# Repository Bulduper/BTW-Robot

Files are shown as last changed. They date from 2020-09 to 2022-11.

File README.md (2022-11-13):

# BTW-Robot
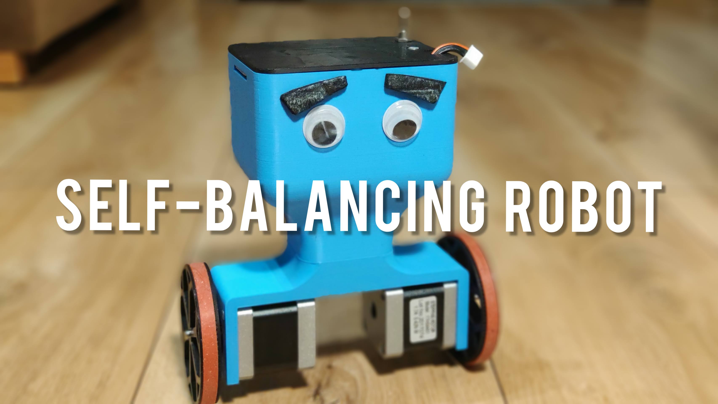
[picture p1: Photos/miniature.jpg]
Photo of robot Balancing robot


## [YouTube video](https://www.youtube.com/watch?v=bfnd0wN4B1s)
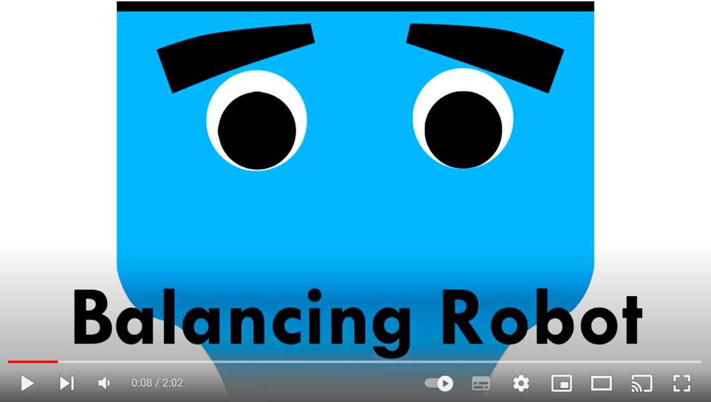
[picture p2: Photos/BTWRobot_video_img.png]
YouTube video (https://www.youtube.com/watch?v=bfnd0wN4B1s)

## Balancing Two-Wheeled Robot
This repository contains all the code files for ESP8266 microcontroller regarding the BTW-Robot project. 

The other part of code is the *android app* to control the robot remotely. [LINK TO REPO](https://github.com/Bulduper/BTW-Robot-Android-App) 

## A short description

The main working principle of a self-balancing robot is to continuously adjust its movement in order to maintain a specific position and/or velocity. 

The BTW-Robot utilizes two stepper motors which are driven to counteract its inertial movement.

## Sensor

The most important information for such a robot is the current angular position.
To get angle data I used MPU6050 inertial measurement unit. The sensor consists of both gyroscope and accelerometer (both 3 Axis).

### Accelerometer
Accelerometer measures acceleration and since under **relatively static** conditions the only significant acceleration is gravitational, we can use that measurement to estimate the tilt angle of the robot.

### Gyroscope
Although the accelerometer would give us a pretty decent estimation of angle in static conditions, the method fails if any oscillations occur.

Gyro measures angular velocity and it does so quite precisely. Precisely enough to be the only source of inertial measurements for our purpouse.
However there are two reasons we cannot use the gyro data alone:
- angular velocity is the derivative of angle and derivatives give no information about starting position. At least once we need to know actual angle, then we could rely on velocity
- gyro measurements tend to drift due to various long term noise (like Coriolis force), so even when no movement the sensor would show changing angle value over time

### Complementary filter
An easy, yet very effective solution is to combine accelerometer and gyro data.
Accelerometer doesn't like high frequecies so we'll give it a low-pass filter.
Gyro doesn't like low frequencies so we'll implement a high-pass filter.
```
angle = c * (angle + gyro * dt) + (1 - c) * accelerometer 
```
where ```c``` would be around 0.98 (depends on time constant).

The above solution is called complementary filter.

## Regulation algorithm
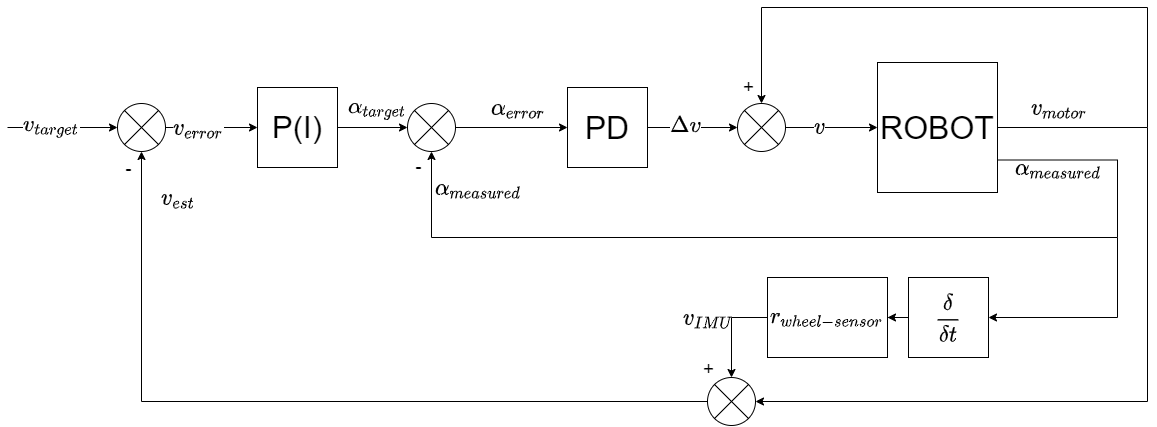
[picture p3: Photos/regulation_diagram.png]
Diagram Regulation algorithm diagram


We've got two closed-loop PID regulators working together in a cascade. The input for the outer regulator is speed error. Error is obtained by subtracting target value and estimated velocity value. The latter involves both absolute motor speed and relative head's speed. This way we can effectively take into account robot tilting as well.
  
## Remote control & telemetry
I used WiFi feature of ESP8266 to remotely control the robot.
Android app sends JSON packets containing steering data via UDP protocol to the ESP. In return ESP sends packets containing speed and tilt values the same way.

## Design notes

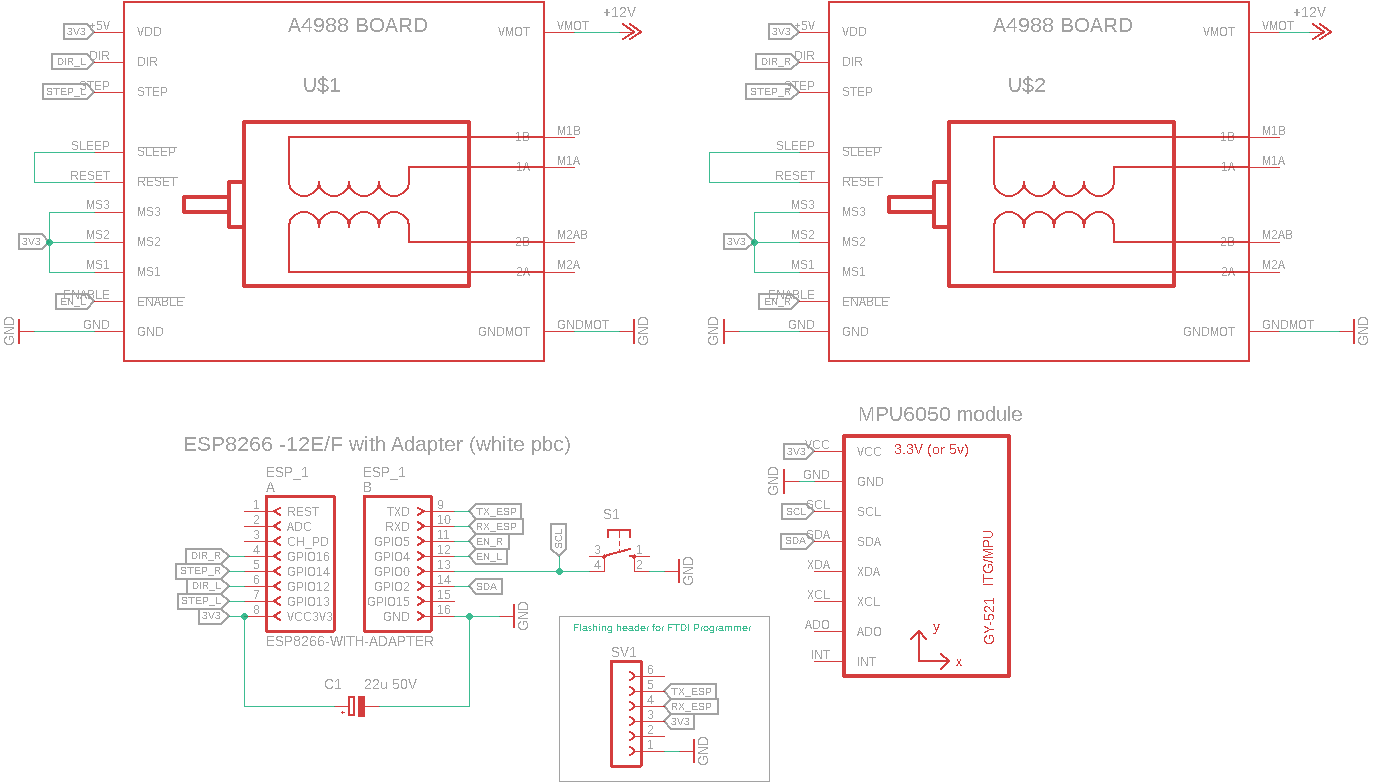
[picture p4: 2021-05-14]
Schematics/BTW_Robot_schematic.png

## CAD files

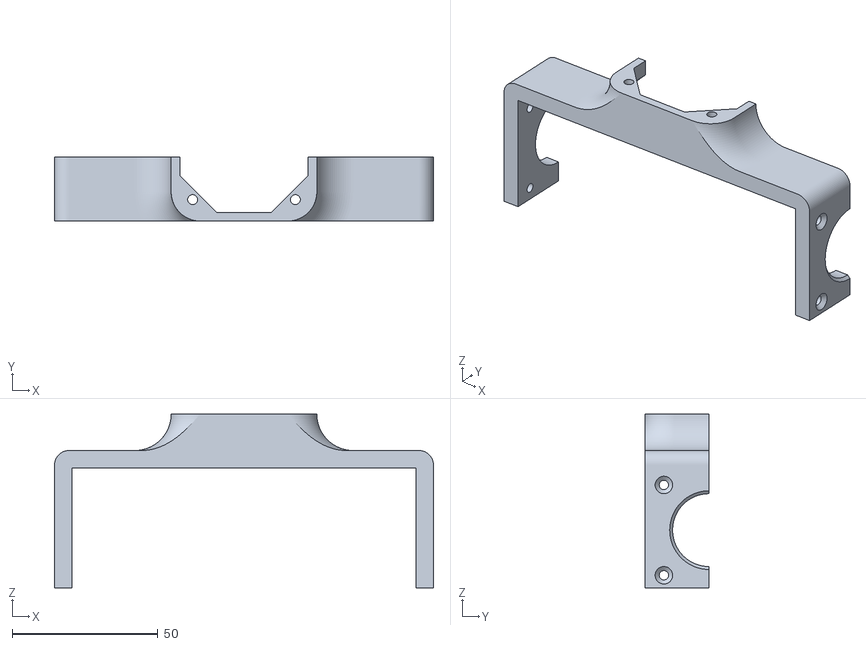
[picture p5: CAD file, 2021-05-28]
STL Files/main_bottom_oneHalf.stl
130.1 x 22.0 x 59.7

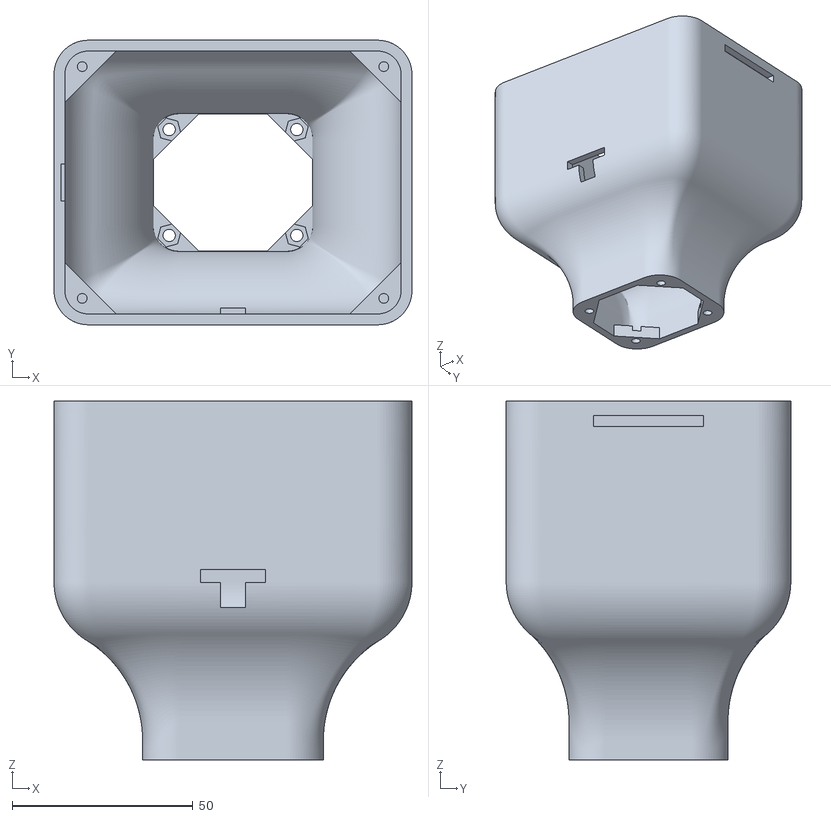
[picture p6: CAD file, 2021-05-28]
STL Files/main_top_v2.2.stl
99.0 x 78.7 x 99.2

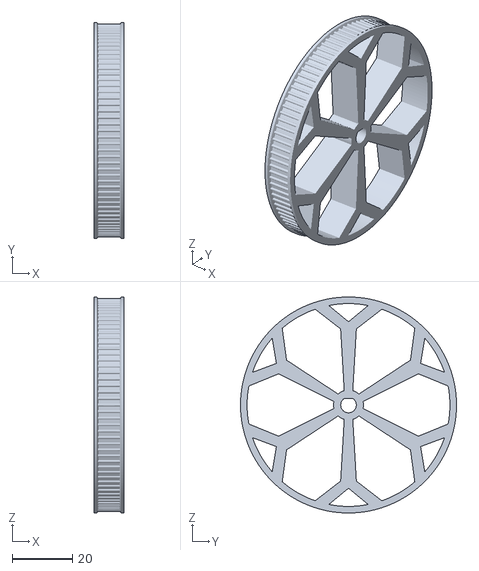
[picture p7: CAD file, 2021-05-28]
STL Files/wheel.stl
10.0 x 72.0 x 72.0

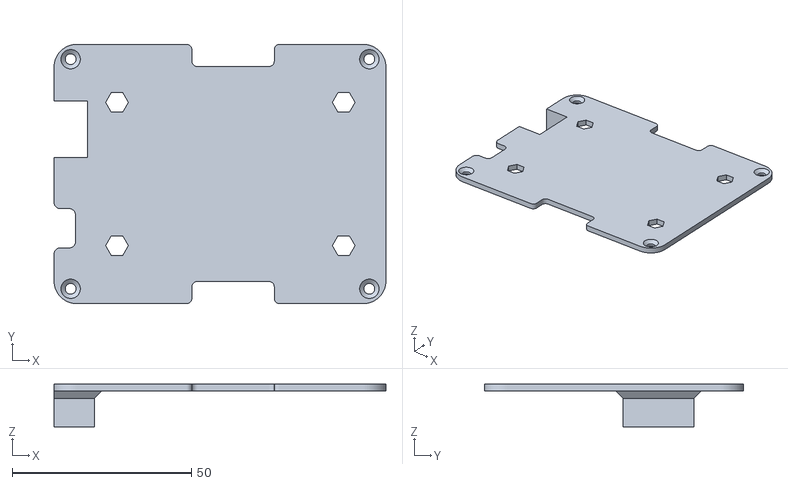
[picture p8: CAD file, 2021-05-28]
STL Files/shelf_v2.2.stl
92.7 x 72.4 x 12.0

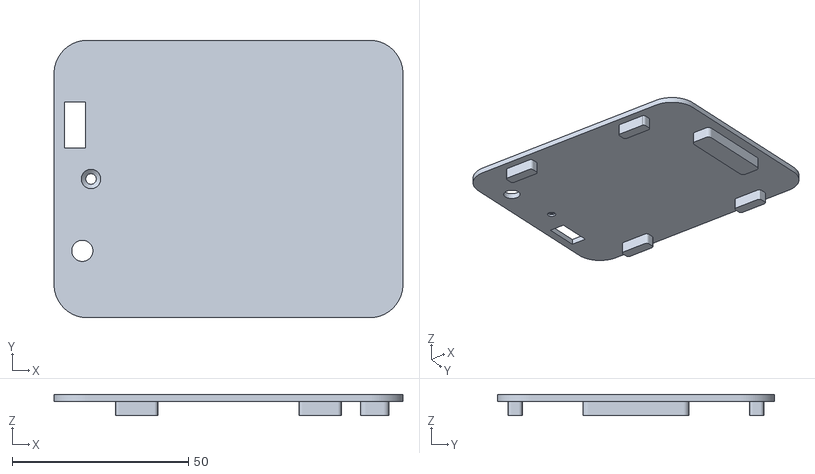
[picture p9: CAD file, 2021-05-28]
STL Files/top_cover_v2.2.stl
99.0 x 78.7 x 6.00

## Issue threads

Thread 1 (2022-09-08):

Code compilation issue with platform io

karthidigi, 2022-09-08:
`lib\ReceivedDataPacket\ReceivedDataPacket.cpp: In member function 'void ReceivedDataPacket::setPacketType()':
lib\ReceivedDataPacket\ReceivedDataPacket.cpp:8:27: error: 'class ArduinoJson6194_F1::StaticJsonDocument<300>' has no member named 'getMember'
    8 |     String pT = getJson().getMember("type");
      |                           ^~~~~~~~~
lib\ReceivedDataPacket\ReceivedDataPacket.cpp: In member function 'void ReceivedDataPacket::setData()':
lib\ReceivedDataPacket\ReceivedDataPacket.cpp:13:22: error: 'class ArduinoJson6194_F1::StaticJsonDocument<300>' has no member named 'getMember'
   13 |     data = getJson().getMember("data");
      |                      ^~~~~~~~~
lib\ReceivedDataPacket\ReceivedDataPacket.cpp: In member function 'String ReceivedDataPacket::getValueString(String)':
lib\ReceivedDataPacket\ReceivedDataPacket.cpp:18:17: error: 'ArduinoJson::JsonObject' {aka 'class ArduinoJson6194_F1::ObjectRef'} has no member named 'getMember'
   18 |     return data.getMember(key);
      |                 ^~~~~~~~~
Compiling .pio\build\nodemcuv2\FrameworkArduino\FunctionalInterrupt.cpp.o
*** [.pio\build\nodemcuv2\lib81a\ReceivedDataPacket\ReceivedDataPacket.cpp.o] Error 1`

Pls help me to debug this issue

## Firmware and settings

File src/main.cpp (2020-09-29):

#include <Arduino.h>
#include <MotorController.h>
#include <BalanceRegulator.h>
#include <WirelessData.h>
#include <PacketCreator.h>
#include <PacketParser.h>
#include <EepromDataHandler.h>

#define stepR 14
#define dirR 16
#define enR 5
#define stepL 13
#define dirL 12
#define enL 4
#define SDA 2
#define SCL 0

BalanceRegulator Regulator;

void loop10Hz();
void sendFeedbackPacket();
void sendTelemetryPacket();
void setTimerInterrupt();
void onDataReceived(char *data);
void setSteeringData(ReceivedDataPacket data);
void setPidValues(ReceivedDataPacket data);
void updateDefaultWifiCredentials(ReceivedDataPacket data);
void setIncomingDataPeriod(ReceivedDataPacket data);
void ICACHE_RAM_ATTR ISR();

bool remoteControllerFound = false;
bool sendTelemetry = false;
String telemetryReceiverIPAddress = "192.168.1.18";
int udpIdealPeriod, udpRealPeriod;

void setup()
{
  //new idea: try to connect to the default wifi (saved in memory), if this will not succeed - set the AP
  //default wifi will be modifable by a json command + reset handling

  Serial.begin(115200);
  motors.begin(stepL, stepR, dirL, dirR, enL, enR, false);

  Wire.begin(SDA, SCL);
  delay(200);
  MPU6050_setup();
  //wireless init part
  EepromDataHandler.init();
  EepromDataHandler.readWifiDataFromEeprom();
  EepromDataHandler.readPidsFromEeprom();
  Regulator.setSpeedPidP(EepromDataHandler.getPids()[0]);
  Regulator.setSpeedPidI(EepromDataHandler.getPids()[1]);
  Regulator.setAnglePidP(EepromDataHandler.getPids()[2]);
  Regulator.setAnglePidD(EepromDataHandler.getPids()[3]);

  if(!WirelessData.connectToWiFi(EepromDataHandler.getSsid(),EepromDataHandler.getPassword()))
  {
    WirelessData.beginAP();
  }

  WirelessData.startUdp(onDataReceived);

  delay(500);
  MPU6050_calibrate();
  setTimerInterrupt();

  motors.readyRoutine();
}

void loop()
{
  WirelessData.loop();
  Regulator.regulateLoop();
  loop10Hz();
}

void setTimerInterrupt()
{
  noInterrupts();
  timer1_isr_init();
  timer1_attachInterrupt(ISR);
  timer1_enable(TIM_DIV1, TIM_EDGE, TIM_LOOP);
  timer1_write(uint32_t(80 * PULSE_PERIOD_us));
  interrupts();
}

void ICACHE_RAM_ATTR ISR()
{
  motors.run();
}

void loop10Hz()
{
  static uint32_t lastT;
  if (micros() - lastT >= 100000)
  {
    if(remoteControllerFound)sendFeedbackPacket();
    if(sendTelemetry)sendTelemetryPacket();
    lastT = micros();
  }
}

void sendFeedbackPacket()
{
  WirelessData.send(PacketCreator::feedbackDataToJsonString(
      Regulator.getLeftVelocity(),
      Regulator.getRightVelocity(),
      Regulator.getCurrentAngle(),
      Regulator.getSpeedPidP(),
      Regulator.getSpeedPidI(),
      Regulator.getAnglePidP(),
      Regulator.getAnglePidD(),
      udpRealPeriod-udpIdealPeriod));
}

void sendTelemetryPacket()
{
  WirelessData.send(PacketCreator::createTelemetryPacket(
      Regulator.getCurrentAngle(),
      Regulator.getRightVelocity(),
      motors.getRPulseInterval()),
    convertIPToInt32(192,168,1,18));
}

void setSteeringData(ReceivedDataPacket data)
{
  Regulator.setRelativeExpectedSpeed(data.getValueInt("throttle"));
  Regulator.setRelativeTurn(data.getValueInt("yaw"));
}

void setPidValues(ReceivedDataPacket data)
{
  Regulator.setSpeedPidP(data.getValueFloat("speedPidP"));
  Regulator.setSpeedPidI(data.getValueFloat("speedPidI"));
  Regulator.setAnglePidP(data.getValueFloat("anglePidP"));
  Regulator.setAnglePidD(data.getValueFloat("anglePidD"));
}

void updateDefaultWifiCredentials(ReceivedDataPacket data)
{
  String ssid, password;
  ssid = data.getValueString("ssid");
  password = data.getValueString("password");
  Serial.printf("New network data - ssid: %s, password: %s\n",ssid.c_str(),password.c_str());
  EepromDataHandler.setSsid(ssid);
  EepromDataHandler.setPassword(password);
  noInterrupts();
  EepromDataHandler.writeWifiDataToEeprom();
  interrupts();
}

void setIncomingDataFPeriod(ReceivedDataPacket data)
{
  udpIdealPeriod = data.getValueInt("interval");
}

void onDataReceived(char *data)
{
  static unsigned int lT;
  udpRealPeriod = millis()-lT;
  lT = millis();

  ReceivedDataPacket dataPacket = PacketParser::stringToJsonData(String(data));
  String receivedDataType = dataPacket.getPacketType();

  if (receivedDataType == "welcome")
  {
    WirelessData.setLastRemoteIpAddress();
    remoteControllerFound = true;
  }
  else if (receivedDataType == "steering")
  {
    setSteeringData(dataPacket);
  }
  else if (receivedDataType == "pids")
  {
    setPidValues(dataPacket);
  }
  else if (receivedDataType == "setNetwork")
  {
    updateDefaultWifiCredentials(dataPacket);
    WirelessData.send(PacketCreator::infoMessageToJsonString("Default Network Updated"));
  }
    else if (receivedDataType == "saveParams")
  {
    EepromDataHandler.setPids(Regulator.getSpeedPidP(),Regulator.getSpeedPidI(),Regulator.getAnglePidP(),Regulator.getAnglePidD());
    noInterrupts();
    EepromDataHandler.writePidsToEeprom();
    interrupts();
    WirelessData.send(PacketCreator::infoMessageToJsonString("PIDs Updated"));
  }
}

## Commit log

2020-09-28 High speed oscilations solved
    [main.cpp]
2021-05-14 Added schematic
    [BTW_Robot.sch]
2021-05-28 STL Files Added
    [main_bottom_oneHalf.stl, main_top_v2.2.stl, shelf_v2.2.stl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]
